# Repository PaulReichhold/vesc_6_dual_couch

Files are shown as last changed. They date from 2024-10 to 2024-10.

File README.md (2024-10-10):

# Compact High Power Motor Controller
Based on the VESC-Project of Benjamin Vedder

## Specs
| Spec | Tested to |
|---|---|
|__Voltage:__| 6.5V - 50.4V |
|__max Phase Current:__| 180A |
|__max Power (dual, with active cooling)__| 15kW |

> [!NOTE]
> One side has the current measurment inverted (forgot which one it was)

> [!WARNING]
> Use the provided design at your own risk

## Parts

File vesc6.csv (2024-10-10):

Source: | C:\Users\paulr\vesc_6_2\vesc6.kicad_sch
Date: | 16.02.2024 15:32:52
Tool: | Eeschema 7.0.10
Generator: | C:\Program Files\KiCad\7.0\bin\scripting\plugins/bom_csv_grouped_by_value.py
Component Count: | 129
Collated Components:
Item | Qty | Reference(s) | Value | LibPart | Footprint | Datasheet | DNP | LCSC-PN | Voltage
1 | 1 | C3 | 100n | Device:C_Small | Capacitor_SMD:C_0603_1608Metric | ~ |  |  | 50V
2 | 16 | C5, C6, C7, C8, C9, C12, C20, C23, C26, C27, C35, C36, C38, C44, C51, C57 | 100n | Device:C | Capacitor_SMD:C_0603_1608Metric | ~ |  |  | 50V
3 | 2 | C10, C11 | 15p | Device:C | Capacitor_SMD:C_0603_1608Metric | ~ |  |  | 50V
4 | 2 | C13, C14 | 1u | Device:C | Capacitor_SMD:C_0603_1608Metric | ~ |  |  | 50V
5 | 1 | C15 | 6n8 | Device:C | Capacitor_SMD:C_0603_1608Metric | ~ |  |  | 100V
6 | 5 | C16, C17, C18, C21, C33 | 2.2u | Device:C | Capacitor_SMD:C_0805_2012Metric | ~ |  |  | 100V
7 | 1 | C19 | 120p | Device:C | Capacitor_SMD:C_0603_1608Metric | ~ |  |  | 100V
8 | 1 | C22 | 22n | Device:C | Capacitor_SMD:C_0603_1608Metric | ~ |  |  | 100V
9 | 4 | C24, C39, C46, C52 | 15n | Device:C | Capacitor_SMD:C_0603_1608Metric | ~ |  |  | 100V
10 | 3 | C25, C31, C32 | 4.7u | Device:C | Capacitor_SMD:C_1206_3216Metric | ~ |  |  | 100V
11 | 3 | C28, C29, C30 | 220n | Device:C | Capacitor_SMD:C_0805_2012Metric | ~ |  |  | 100V
12 | 2 | C34, C37 | 100u | Device:C_Polarized | Capacitor_Tantalum_SMD:CP_EIA-3528-21_Kemet-B | ~ |  |  | 16V
13 | 3 | C40, C48, C53 | 1n | Device:C | Capacitor_SMD:C_0603_1608Metric | ~ |  |  | 100V
14 | 6 | C41, C42, C49, C50, C54, C55 | 4.7u | Device:C | Capacitor_SMD:C_1210_3225Metric | ~ |  |  | 100V
15 | 3 | C43, C45, C47 | 470u | Device:C_Polarized | Capacitor_THT:CP_Radial_D12.5mm_P5.00mm | ~ |  |  | 80V
16 | 2 | C56, C58 | 22u | Device:C_Polarized | Capacitor_SMD:CP_Elec_8x6.2 | https://datasheet.lcsc.com/lcsc/2304140030_Nichicon-UCD1J220MCL6GS_C445454.pdf |  | C445454 | 63V
17 | 1 | D5 | GRN | Device:LED | LED_SMD:LED_0603_1608Metric_Pad1.05x0.95mm_HandSolder | ~
18 | 1 | D6 | RED | Device:LED | LED_SMD:LED_0603_1608Metric_Pad1.05x0.95mm_HandSolder | ~
19 | 1 | D7 | BLU | Device:LED | LED_SMD:LED_0603_1608Metric_Pad1.05x0.95mm_HandSolder | ~
20 | 1 | D8 | D_Schottky | Device:D_Schottky | Diode_SMD:D_SOD-128 | https://datasheet.lcsc.com/lcsc/2004031108_Nexperia-PMEG10030ELP_C503376.pdf |  | C503376
21 | 1 | D9 | 5V | Device:D_TVS | Diode_SMD:D_SOD-128 | https://datasheet.lcsc.com/lcsc/2304140030_Nexperia-PTVS5V0P1UP-115_C426873.pdf |  | C426873
22 | 1 | FB1 | FerriteBead | Device:FerriteBead | Resistor_SMD:R_1206_3216Metric | https://datasheet.lcsc.com/lcsc/2305221646_YJYCOIN-YI321611U601-3R0T_C2858472.pdf |  | C2858472 | 100V
23 | 1 | J1 | Main | Connector_Generic:Conn_01x03 | Connector_PinSocket_2.54mm:PinSocket_1x03_P2.54mm_Vertical | ~
24 | 1 | J2 | HALL_ENC | Connector_Generic:Conn_01x06 | Connector_JST:JST_PH_B6B-PH-K_1x06_P2.00mm_Vertical | ~
25 | 1 | J6 | USB | Connector:USB_OTG | Connector_USB:USB_Micro-B_Wuerth_614105150721_Vertical_CircularHoles | ~
26 | 1 | L1 | 22u | Device:L | Inductor_SMD:L_Bourns-SRN4018 | https://datasheet.lcsc.com/lcsc/2201121400_SHOU-HAN-CY43-22UH_C2929420.pdf |  | C2929420
27 | 1 | Q1 | DMN62D0UW | Device:Q_NMOS_GSD | Package_TO_SOT_SMD:SOT-323_SC-70 | https://datasheet.lcsc.com/lcsc/2308101701_Diodes-Incorporated-DMN62D0UWQ-7_C5248878.pdf |  | C5248878
28 | 6 | Q2, Q3, Q4, Q5, Q6, Q7 | HYG015N10NS1TA | Device:Q_NMOS_GSD | Package_TO_SOT_SMD:Infineon_PG-HSOF-8-1 | ~ |  | C2979263
29 | 7 | R6, R7, R8, R21, R25, R27, R29 | 2.2k | Device:R | Resistor_SMD:R_0603_1608Metric | ~
30 | 1 | R10 | 0 | Device:R | Resistor_SMD:R_0603_1608Metric | ~
31 | 3 | R11, R23, R30 | 10k | Device:R | Resistor_SMD:R_0603_1608Metric | ~
32 | 2 | R12, R13 | 22 | Device:R | Resistor_SMD:R_0603_1608Metric | ~
33 | 2 | R14, R15 | 220 | Device:R | Resistor_SMD:R_0603_1608Metric | ~
34 | 4 | R16, R34, R38, R40 | 1k | Device:R | Resistor_SMD:R_0603_1608Metric | ~
35 | 1 | R17 | 3.3k | Device:R | Resistor_SMD:R_0603_1608Metric | ~
36 | 1 | R18 | 18k | Device:R | Resistor_SMD:R_0603_1608Metric | ~
37 | 1 | R19 | 15k | Device:R | Resistor_SMD:R_0603_1608Metric | ~
38 | 3 | R20, R24, R26 | 39k | Device:R | Resistor_SMD:R_0603_1608Metric | ~
39 | 1 | R22 | 220k | Device:R | Resistor_SMD:R_0603_1608Metric | ~
40 | 1 | R28 | 39K | Device:R | Resistor_SMD:R_0603_1608Metric | ~
41 | 3 | R31, R35, R39 | 0.5m | Device:R_Shunt | TUWR_Sensors:BVN_1216 | https://datasheet.lcsc.com/lcsc/2103091535_Isabellenhuette-BVN-Z-R0005-1-0_C2688874.pdf |  | C2688874
42 | 6 | R32, R33, R36, R37, R41, R42 | 4.7 | Device:R | Resistor_SMD:R_0603_1608Metric | ~
43 | 1 | R43 | 120 | Device:R | Resistor_SMD:R_0603_1608Metric | ~
44 | 1 | SW1 | SENS_VOLTAGE | Switch:SW_Push_SPDT | Jumper:SolderJumper-3_P1.3mm_Bridged2Bar12_Pad1.0x1.5mm | ~
45 | 1 | TH1 | NTC | Device:Thermistor_NTC | Connector_PinHeader_1.27mm:PinHeader_1x02_P1.27mm_Vertical | ~
46 | 1 | TP1 | SWCLK | Connector:TestPoint | TestPoint:TestPoint_Pad_D1.0mm | ~
47 | 1 | TP2 | SWDIO | Connector:TestPoint | TestPoint:TestPoint_Pad_D1.0mm | ~
48 | 1 | TP3 | NRST | Connector:TestPoint | TestPoint:TestPoint_Pad_D1.0mm | ~
49 | 1 | TP4 | GND | Connector:TestPoint | TestPoint:TestPoint_Pad_D1.0mm | ~
50 | 1 | U1 | STM32F405RGTx | MCU_ST_STM32F4:STM32F405RGTx | Package_QFP:LQFP-64_10x10mm_P0.5mm | http://www.st.com/st-web-ui/static/active/en/resource/technical/document/datasheet/DM00037051.pdf |  | C15742
51 | 6 | U2, U4, U5, U8, U9, U11 | Mc74VHC1GT66 | TUWR_IC:Mc74VHC1GT66 | Package_TO_SOT_SMD:SOT-353_SC-70-5 | https://www.lcsc.com/product-detail/span-style-background-color-ff0-Analog-span-Switches-Multiplexers_Texas-Instruments-SN74LVC1G66DCKR_C113518.html |  | C113518
52 | 1 | U3 | DRV8301DCAR | 2023-03-11_13-45-03:DRV8301DCAR | Package_SO:HTSSOP-56-1EP_6.1x14mm_P0.5mm_EP3.61x6.35mm | https://datasheet.lcsc.com/lcsc/1808280253_Texas-Instruments-DRV8301DCAR_C98969.pdf |  | C98969
53 | 1 | U6 | TLV73333PDBV | Regulator_Linear:TLV73333PDBV | Package_TO_SOT_SMD:SOT-23-5 | http://www.ti.com/lit/ds/symlink/tlv733p.pdf |  | C134139
54 | 3 | U7, U10, U12 | AD8418 | Amplifier_Current:AD8418 | Package_SO:MSOP-8_3x3mm_P0.65mm | https://www.analog.com/media/en/technical-documentation/data-sheets/AD8418.pdf |  | C147928
55 | 1 | U14 | SN65HVD232 | Interface_CAN_LIN:SN65HVD232 | Package_SO:SOIC-8_3.9x4.9mm_P1.27mm | https://datasheet.lcsc.com/lcsc/1810181615_Texas-Instruments-SN65HVD232DR_C30530.pdf |  | C30530
56 | 1 | Y1 | 8M | Device:Crystal_GND24 | Crystal:Crystal_SMD_EuroQuartz_MT-4Pin_3.2x2.5mm_HandSoldering | ~

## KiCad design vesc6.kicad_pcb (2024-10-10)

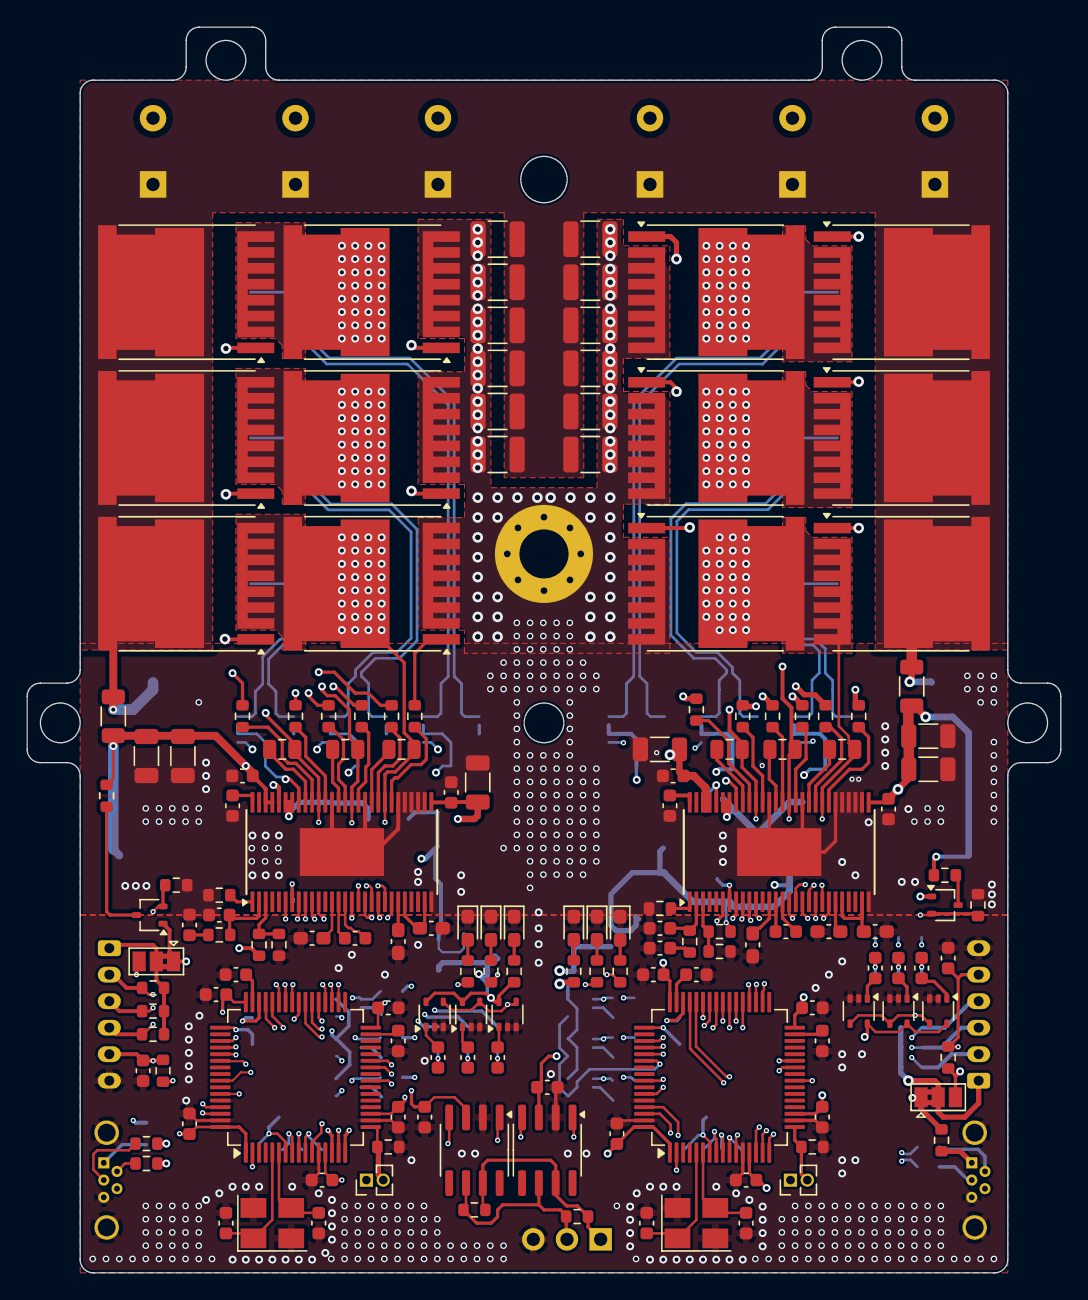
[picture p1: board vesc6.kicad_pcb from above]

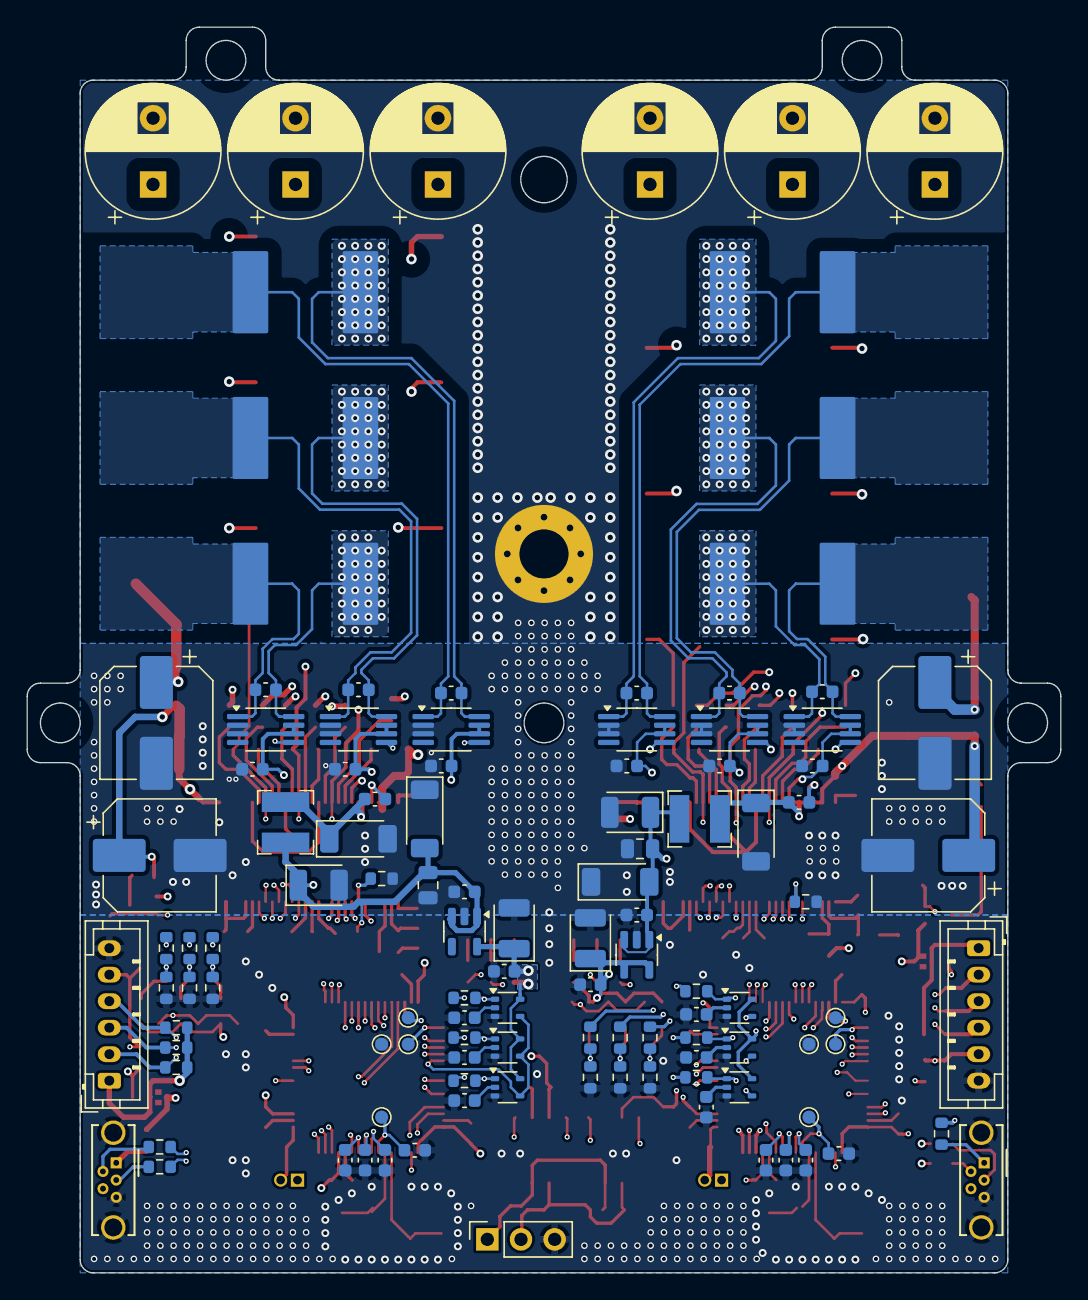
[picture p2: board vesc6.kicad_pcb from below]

Board: 4 copper layers, 78.0 x 94.0 mm, 266 parts (113 on the bottom side), 190 nets.

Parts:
C1, C2, C3, C4, C5, C6, C7, C8, C9, C12, C20, C23, C26, C27, C35, C36, C38, C44, C51, C57, C59, C69, C77, C82, C83, C84, C85, C86, C89, C94, C99, C101, C102, C106, C108, C114, C116, C118: 100n; C_0603_1608Metric
C10, C11, C87, C88: 15p; C_0603_1608Metric
C13, C14, C90, C91: 1u; C_0603_1608Metric
C15, C93: 6n8; C_0603_1608Metric
C16, C40, C48, C53, C61, C62, C63, C64, C68, C73, C76, C79: 1n; C_0603_1608Metric
C17, C18, C21, C92, C96, C98: 2.2u; C_0603_1608Metric_Pad1.08x0.95mm_HandSolder
C19, C97: 120p; C_0603_1608Metric
C22, C95: 22n; C_0603_1608Metric
C24, C39, C46, C52, C60, C71, C78, C100: 15n; C_0603_1608Metric
C25, C31, C32, C107, C109, C110: 4.7u; C_1206_3216Metric
C28, C29, C30, C103, C104, C105: 220n; C_0805_2012Metric
C33, C111: 2.2u; C_0805_2012Metric
C34, C37, C113, C117: 100u; CP_EIA-3528-21_Kemet-B
C41, C42, C49, C50, C54, C55, C65, C66, C74, C75, C80, C81: 4.7u; C_1210_3225Metric
C43, C45, C47, C67, C70, C72: 470u; CP_Radial_D10.0mm_P5.00mm
C56, C58, C112, C115: 22u; CP_Elec_8x6.2
D1, D5: GRN; LED_0603_1608Metric_Pad1.05x0.95mm_HandSolder
D2, D6: RED; LED_0603_1608Metric_Pad1.05x0.95mm_HandSolder
D3, D7: BLU; LED_0603_1608Metric_Pad1.05x0.95mm_HandSolder
D4, D8: D_Schottky; D_SOD-128
D9, D10: 5V; D_SOD-128
FB1, FB2: FerriteBead; R_1206_3216Metric
H1: MountingHole_Pad; MountingHole_3.7mm_Pad_Via
J1: Main; PinSocket_1x03_P2.54mm_Vertical
J2, J3: HALL_ENC; JST_PH_B6B-PH-K_1x06_P2.00mm_Vertical
J4, J6: USB; USB_Micro-B_Wuerth_614105150721_Vertical_CircularHoles
L1, L2: 22u; L_Bourns-SRN4018
Q1, Q14: DMN62D0UW; SOT-323_SC-70
Q2, Q3, Q4, Q5, Q6, Q7, Q8, Q9, Q10, Q11, Q12, Q13: HYG015N10NS1TA; Infineon_PG-HSOF-8-1
R1, R2, R3, R49, R53, R57: 0.5m; WSLP3921
R4, R5, R6, R7, R8, R9, R21, R25, R27, R29, R65, R69, R71, R73: 2.2k; R_0603_1608Metric
R10, R31: 0; R_0603_1608Metric
R11, R23, R30, R35, R48, R67: 10k; R_0603_1608Metric
R12, R13, R39, R44: 22; R_0603_1608Metric
R14, R15, R45, R46: 220; R_0603_1608Metric
R16, R34, R38, R40, R47, R52, R56, R58: 1k; R_0603_1608Metric
R17, R61: 3.3k; R_0603_1608Metric
R18, R62: 18k; R_0603_1608Metric
R19, R63: 15k; R_0603_1608Metric
R20, R24, R26, R64, R68, R70: 39k; R_0603_1608Metric
R22, R66: 220k; R_0603_1608Metric
R28, R72: 39K; R_0603_1608Metric
R32, R33, R36, R37, R41, R42, R50, R51, R54, R55, R59, R60: 4.7; R_0603_1608Metric
R43, R74: 120; R_0603_1608Metric
SW1, SW2: SENS_VOLTAGE; SolderJumper-3_P1.3mm_Bridged2Bar12_Pad1.0x1.5mm
TH1, TH2: NTC; PinHeader_1x02_P1.27mm_Vertical
TP1, TP5: SWCLK; TestPoint_Pad_D1.0mm
TP2, TP6: SWDIO; TestPoint_Pad_D1.0mm
TP3, TP7: NRST; TestPoint_Pad_D1.0mm
TP4, TP8: GND; TestPoint_Pad_D1.0mm
U1, U20: STM32F405RGTx; LQFP-64_10x10mm_P0.5mm
U2, U4, U5, U8, U9, U11, U15, U16, U18, U21, U23, U24: Mc74VHC1GT66; SOT-353_SC-70-5
U3, U22: DRV8301DCAR; HTSSOP-56-1EP_6.1x14mm_P0.5mm_EP3.61x6.35mm
U6, U25: TLV73333PDBV; SOT-23-5
U7, U10, U12, U13, U17, U19: AD8418; MSOP-8_3x3mm_P0.65mm
U14, U26: SN65HVD232; SOIC-8_3.9x4.9mm_P1.27mm
Y1, Y2: 8M; Crystal_SMD_EuroQuartz_MT-4Pin_3.2x2.5mm_HandSoldering

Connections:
/VESC_Left/3.3V: C5.1, C6.1, C7.1, C8.1, C9.1, C36.1, C37.1, C38.2, C44.2, C51.2, C57.1, R11.2, R16.2, SW1.3 (C), TH1.1, U1.1 (VBAT), U1.13 (VDDA), U1.19 (VDD), U1.32 (VDD), U1.48 (VDD), U1.64 (VDD), U2.5 (VCC), U3.49 (VDD_SPI), U4.5 (VCC), U5.5 (VCC), U6.5 (OUT), U7.6 (VS), U7.7 (REF1), U8.5 (VCC), U9.5 (VCC), U10.6 (VS), U10.7 (REF1), U11.5 (VCC), U12.6 (VS), U12.7 (REF1), U14.3 (VCC)
/VESC_Left/5V: C33.1, C34.1, C35.1, D9.2 (A2), L1.2, Q1.1 (G), R10.2, R18.2, SW1.1 (A), U6.1 (IN), U6.3 (EN)
/VESC_Left/CAN/RX: U1.61 (PB8), U14.4 (R)
/VESC_Left/CAN/TX: U1.62 (PB9), U14.1 (D)
/VESC_Left/CAN_H: J1.1, R43.1, R74.1, U14.7 (CANH), U26.7 (CANH)
/VESC_Left/CAN_L: J1.2, R43.2, R74.2, U14.6 (CANL), U26.6 (CANL)
/VESC_Left/DRV8301/CS: U1.40 (PC9), U3.8 (*SCS)
/VESC_Left/DRV8301/EN_GATE: U1.57 (PB5), U3.16 (EN_GATE)
/VESC_Left/DRV8301/FAULT: U1.59 (PB7), U3.6 (*FAULT)
/VESC_Left/DRV8301/GH_A: R32.1, U3.47 (GH_A)
/VESC_Left/DRV8301/GH_B: R36.1, U3.42 (GH_B)
/VESC_Left/DRV8301/GH_C: R41.1, U3.37 (GH_C)
/VESC_Left/DRV8301/GL_A: R33.1, U3.45 (GL_A)
/VESC_Left/DRV8301/GL_B: R37.1, U3.40 (GL_B)
/VESC_Left/DRV8301/GL_C: R42.1, U3.35 (GL_C)
/VESC_Left/DRV8301/INH_A: U1.41 (PA8), U3.17 (INH_A)
/VESC_Left/DRV8301/INH_B: U1.42 (PA9), U3.19 (INH_B)
/VESC_Left/DRV8301/INH_C: U1.43 (PA10), U3.21 (INH_C)
/VESC_Left/DRV8301/INL_A: U1.34 (PB13), U3.18 (INL_A)
/VESC_Left/DRV8301/INL_B: U1.35 (PB14), U3.20 (INL_B)
/VESC_Left/DRV8301/INL_C: U1.36 (PB15), U3.22 (INL_C)
/VESC_Left/DRV8301/SCLK: U1.51 (PC10), U3.11 (SCLK)
/VESC_Left/DRV8301/SDI: U1.53 (PC12), U3.9 (SDI)
/VESC_Left/DRV8301/SDO: U1.52 (PC11), U3.10 (SDO)
/VESC_Left/DRV8301/SENS_A: C20.1, R20.2, R21.2, U1.14 (PA0)
/VESC_Left/DRV8301/SENS_B: C23.1, R24.2, R25.2, U1.15 (PA1)
/VESC_Left/DRV8301/SENS_C: C26.1, R26.2, R27.2, U1.16 (PA2)
/VESC_Left/DRV8301/SENS_FILTERED: U1.2 (PC13), U2.4 (ON_OFF), U4.4 (ON_OFF), U5.4 (ON_OFF)
/VESC_Left/DRV8301/SENS_SUPPLY: Q1.2 (S), R29.1, U1.11 (PC3)
/VESC_Left/DRV8301/Supply_Filterted: C1.1, C2.1, C25.1, C31.1, C32.1, C58.1, FB1.1, R28.1, U3.29 (PVDD1), U3.53 (PVDD2), U3.54 (PVDD2)
/VESC_Left/MCU/ADC_TEMP: R30.2, TH1.2, U1.17 (PA3)
/VESC_Left/MCU/CURRENT_1: C40.2, R34.1, U1.8 (PC0), U8.1 (IO_XA)
/VESC_Left/MCU/CURRENT_2: C48.2, R38.1, U1.9 (PC1), U9.1 (IO_XA)
/VESC_Left/MCU/CURRENT_3: C53.2, R40.1, U1.10 (PC2), U11.1 (IO_XA)
/VESC_Left/MCU/CURR_FILTER_ON: U1.54 (PD2), U8.4 (ON_OFF), U9.4 (ON_OFF), U11.4 (ON_OFF)
/VESC_Left/MCU/HALL_1: J2.2, R6.2, U1.37 (PC6)
/VESC_Left/MCU/HALL_2: J2.3, R7.2, U1.38 (PC7)
/VESC_Left/MCU/HALL_3: J2.4, R8.2, U1.39 (PC8)
/VESC_Left/MCU/LED_GREEN: R14.2, U1.26 (PB0)
/VESC_Left/MCU/LED_RED: R15.2, U1.27 (PB1)
/VESC_Left/MCU/NRST: C12.1, TP3.1, U1.7 (NRST)
/VESC_Left/MCU/SWCLK: TP1.1, U1.49 (PA14)
/VESC_Left/MCU/SWDIO: TP2.1, U1.46 (PA13)
/VESC_Left/MCU/TEMP_MOTOR: C3.1, J2.5, R11.1, U1.24 (PC4)
/VESC_Left/MCU/USB_D_N: R13.2, U1.44 (PA11)
/VESC_Left/MCU/USB_D_P: R12.2, U1.45 (PA12)
/VESC_Left/Power_alternate/C_A: R34.2, U7.5 (OUT)
/VESC_Left/Power_alternate/C_B: R38.2, U10.5 (OUT)
/VESC_Left/Power_alternate/C_C: R40.2, U12.5 (OUT)
/VESC_Left/Power_alternate/SH_A_N: C61.1, R1.2, U7.1 (IN-)
/VESC_Left/Power_alternate/SH_A_P: C28.1, C61.2, Q2.2 (S), Q3.3 (D), R1.1, R20.1, U3.46 (SH_A), U7.8 (IN+)
/VESC_Left/Power_alternate/SH_B_N: C62.1, R2.2, U10.1 (IN-)
/VESC_Left/Power_alternate/SH_B_P: C29.1, C62.2, Q4.2 (S), Q5.3 (D), R2.1, R24.1, U3.41 (SH_B), U10.8 (IN+)
/VESC_Left/Power_alternate/SH_C_N: C63.1, R3.2, U12.1 (IN-)
/VESC_Left/Power_alternate/SH_C_P: C30.1, C63.2, Q6.2 (S), Q7.3 (D), R3.1, R26.1, U3.36 (SH_C), U12.8 (IN+)
/VESC_Left/SUPPLY: C41.1, C42.1, C43.1, C45.1, C47.1, C49.1, C50.1, C54.1, C55.1, C56.1, C65.1, C66.1, C67.1, C70.1, C72.1, C74.1, C75.1, C80.1, C81.1, C115.1, FB1.2, FB2.2, Q2.3 (D), Q4.3 (D), Q6.3 (D), Q8.3 (D), Q10.3 (D), Q12.3 (D)
/VESC_Right/3.3V: C59.2, C69.2, C77.2, C82.1, C83.1, C84.1, C85.1, C86.1, C116.1, C117.1, C118.1, R35.2, R47.2, SW2.3 (C), TH2.1, U13.6 (VS), U13.7 (REF1), U15.5 (VCC), U16.5 (VCC), U17.6 (VS), U17.7 (REF1), U18.5 (VCC), U19.6 (VS), U19.7 (REF1), U20.1 (VBAT), U20.13 (VDDA), U20.19 (VDD), U20.32 (VDD), U20.48 (VDD), U20.64 (VDD), U21.5 (VCC), U22.49 (VDD_SPI), U23.5 (VCC), U24.5 (VCC), U25.5 (OUT), U26.3 (VCC)
/VESC_Right/5V: C111.1, C113.1, C114.1, D10.2 (A2), L2.2, Q14.1 (G), R31.2, R62.2, SW2.1 (A), U25.1 (IN), U25.3 (EN)
/VESC_Right/CAN/RX: U20.61 (PB8), U26.4 (R)
/VESC_Right/CAN/TX: U20.62 (PB9), U26.1 (D)
/VESC_Right/DRV8301/CS: U20.40 (PC9), U22.8 (*SCS)
/VESC_Right/DRV8301/EN_GATE: U20.57 (PB5), U22.16 (EN_GATE)
/VESC_Right/DRV8301/FAULT: U20.59 (PB7), U22.6 (*FAULT)
/VESC_Right/DRV8301/GH_A: R50.1, U22.47 (GH_A)
/VESC_Right/DRV8301/GH_B: R54.1, U22.42 (GH_B)
/VESC_Right/DRV8301/GH_C: R59.1, U22.37 (GH_C)
/VESC_Right/DRV8301/GL_A: R51.1, U22.45 (GL_A)
/VESC_Right/DRV8301/GL_B: R55.1, U22.40 (GL_B)
/VESC_Right/DRV8301/GL_C: R60.1, U22.35 (GL_C)
/VESC_Right/DRV8301/INH_A: U20.41 (PA8), U22.17 (INH_A)
/VESC_Right/DRV8301/INH_B: U20.42 (PA9), U22.19 (INH_B)
/VESC_Right/DRV8301/INH_C: U20.43 (PA10), U22.21 (INH_C)
/VESC_Right/DRV8301/INL_A: U20.34 (PB13), U22.18 (INL_A)
/VESC_Right/DRV8301/INL_B: U20.35 (PB14), U22.20 (INL_B)
/VESC_Right/DRV8301/INL_C: U20.36 (PB15), U22.22 (INL_C)
/VESC_Right/DRV8301/SCLK: U20.51 (PC10), U22.11 (SCLK)
/VESC_Right/DRV8301/SDI: U20.53 (PC12), U22.9 (SDI)
/VESC_Right/DRV8301/SDO: U20.52 (PC11), U22.10 (SDO)
/VESC_Right/DRV8301/SENS_A: C94.1, R64.2, R65.2, U20.14 (PA0)
/VESC_Right/DRV8301/SENS_B: C99.1, R68.2, R69.2, U20.15 (PA1)
/VESC_Right/DRV8301/SENS_C: C101.1, R70.2, R71.2, U20.16 (PA2)
/VESC_Right/DRV8301/SENS_FILTERED: U20.2 (PC13), U21.4 (ON_OFF), U23.4 (ON_OFF), U24.4 (ON_OFF)
/VESC_Right/DRV8301/SENS_SUPPLY: Q14.2 (S), R73.1, U20.11 (PC3)
/VESC_Right/DRV8301/Supply_Filterted: C106.1, C107.1, C108.1, C109.1, C110.1, C112.1, FB2.1, R72.1, U22.29 (PVDD1), U22.53 (PVDD2), U22.54 (PVDD2)
/VESC_Right/MCU/ADC_TEMP: R48.2, TH2.2, U20.17 (PA3)
/VESC_Right/MCU/CURRENT_1: C64.2, R52.1, U15.1 (IO_XA), U20.8 (PC0)
/VESC_Right/MCU/CURRENT_2: C73.2, R56.1, U16.1 (IO_XA), U20.9 (PC1)
/VESC_Right/MCU/CURRENT_3: C79.2, R58.1, U18.1 (IO_XA), U20.10 (PC2)
/VESC_Right/MCU/CURR_FILTER_ON: U15.4 (ON_OFF), U16.4 (ON_OFF), U18.4 (ON_OFF), U20.54 (PD2)
/VESC_Right/MCU/HALL_1: J3.2, R4.2, U20.37 (PC6)
/VESC_Right/MCU/HALL_2: J3.3, R5.2, U20.38 (PC7)
/VESC_Right/MCU/HALL_3: J3.4, R9.2, U20.39 (PC8)
/VESC_Right/MCU/LED_GREEN: R45.2, U20.26 (PB0)
/VESC_Right/MCU/LED_RED: R46.2, U20.27 (PB1)
/VESC_Right/MCU/NRST: C89.1, TP7.1, U20.7 (NRST)
/VESC_Right/MCU/SWCLK: TP5.1, U20.49 (PA14)
/VESC_Right/MCU/SWDIO: TP6.1, U20.46 (PA13)
/VESC_Right/MCU/TEMP_MOTOR: C4.1, J3.5, R35.1, U20.24 (PC4)
/VESC_Right/MCU/USB_D_N: R44.2, U20.44 (PA11)
/VESC_Right/MCU/USB_D_P: R39.2, U20.45 (PA12)
/VESC_Right/Power/C_A: R52.2, U13.5 (OUT)
/VESC_Right/Power/C_B: R56.2, U17.5 (OUT)
/VESC_Right/Power/C_C: R58.2, U19.5 (OUT)
/VESC_Right/Power/SH_A_N: C16.2, R57.2, U13.8 (IN+)
/VESC_Right/Power/SH_A_P: C16.1, C103.1, Q8.2 (S), Q9.3 (D), R57.1, R64.1, U13.1 (IN-), U22.46 (SH_A)
/VESC_Right/Power/SH_B_N: C68.2, R53.2, U17.8 (IN+)
/VESC_Right/Power/SH_B_P: C68.1, C104.1, Q10.2 (S), Q11.3 (D), R53.1, R68.1, U17.1 (IN-), U22.41 (SH_B)
/VESC_Right/Power/SH_C_N: C76.2, R49.2, U19.8 (IN+)
/VESC_Right/Power/SH_C_P: C76.1, C105.1, Q12.2 (S), Q13.3 (D), R49.1, R70.1, U19.1 (IN-), U22.36 (SH_C)
GND: C1.2, C2.2, C3.2, C4.2, C5.2, C6.2, C7.2, C8.2, C9.2, C10.2, C11.2, C12.2, C13.2, C14.2, C15.2, C17.2, C18.2, C19.2, C21.2, C24.1, C25.2, C31.2, C32.2, C33.2, C34.2, C35.2, C36.2, C37.2, C38.1, C39.1, C40.1, C41.2, C42.2, C43.2, C44.1, C45.2, C46.1, C47.2, C48.1, C49.2, C50.2, C51.1, C52.1, C53.1, C54.2, C55.2, C56.2, C57.2, C58.2, C59.1, C60.1, C64.1, C65.2, C66.2, C67.2, C69.1, C70.2, C71.1, C72.2, C73.1, C74.2, C75.2, C77.1, C78.1, C79.1, C80.2, C81.2, C82.2, C83.2, C84.2, C85.2, C86.2, C87.2, C88.2, C89.2, C90.2, C91.2, C92.2, C93.2, C96.2, C97.2, C98.2, C100.1, C106.2, C107.2, C108.2, C109.2, C110.2, C111.2, C112.2, C113.2, C114.2, C115.2, C116.2, C117.2, C118.2, D1.1 (K), D2.1 (K), D3.1 (K), D4.2 (A), D5.1 (K), D6.1 (K), D7.1 (K), D8.2 (A), D9.1 (A1), D10.1 (A1), H1.1, J1.3, J2.6, J3.6, J4.5 (GND), J4.6 (Shield), J6.5 (GND), J6.6 (Shield), Q3.2 (S), Q5.2 (S), Q7.2 (S), Q9.2 (S), Q11.2 (S), Q13.2 (S), R17.1, R21.1, R22.1, R23.2, R25.1, R27.1, R29.2, R30.1, R48.1, R61.1, R65.1, R66.1, R67.2, R69.1, R71.1, R73.2, TP4.1, TP8.1, U1.12 (VSSA), U1.18 (VSS), U1.60 (BOOT0), U1.63 (VSS), U2.2 (IO_YA), U2.3 (GND), U3.28 (AGND), U3.30 (SP2), U3.31 (SN2), U3.32 (SP1), U3.33 (SN1), U3.34 (SL_C), U3.39 (SL_B), U3.44 (SL_A), U3.57 (EPAD), U4.2 (IO_YA), U4.3 (GND), U5.2 (IO_YA), U5.3 (GND), U6.2 (GND), U7.2 (GND), U7.3 (REF2), U8.3 (GND), U9.3 (GND), U10.2 (GND), U10.3 (REF2), U11.3 (GND), U12.2 (GND), U12.3 (REF2), U13.2 (GND), U13.3 (REF2), U14.2 (GND), U15.3 (GND), U16.3 (GND), U17.2 (GND), U17.3 (REF2), U18.3 (GND), U19.2 (GND), U19.3 (REF2), U20.12 (VSSA), U20.18 (VSS), U20.60 (BOOT0), U20.63 (VSS), U21.2 (IO_YA), U21.3 (GND), U22.28 (AGND), U22.30 (SP2), U22.31 (SN2), U22.32 (SP1), U22.33 (SN1), U22.34 (SL_C), U22.39 (SL_B), U22.44 (SL_A), U22.57 (EPAD), U23.2 (IO_YA), U23.3 (GND), U24.2 (IO_YA), U24.3 (GND), U25.2 (GND), U26.2 (GND), Y1.2, Y1.4, Y2.2, Y2.4
unnamed: C15.1, R19.1
unnamed: C93.1, R63.1
unnamed: D1.2 (A), R45.1
unnamed: D2.2 (A), R46.1
unnamed: D3.2 (A), R47.1
unnamed: C102.1, D4.1 (K), L2.1, U22.50 (PH), U22.51 (PH)
unnamed: D5.2 (A), R14.1
unnamed: D6.2 (A), R15.1
unnamed: D7.2 (A), R16.1
unnamed: C27.1, D8.1 (K), L1.1, U3.50 (PH), U3.51 (PH)
unnamed: J2.1, R6.1, R7.1, R8.1, SW1.2 (B)
unnamed: J3.1, R4.1, R5.1, R9.1, SW2.2 (B)
unnamed: J4.3 (D+), R39.1
unnamed: J4.2 (D-), R44.1
unnamed: J4.1 (VBUS), R31.1
unnamed: J6.3 (D+), R12.1
unnamed: J6.2 (D-), R13.1
unnamed: J6.1 (VBUS), R10.1
unnamed: Q1.3 (D), R28.2
unnamed: Q2.1 (G), R32.2
unnamed: Q3.1 (G), R33.2
unnamed: Q4.1 (G), R36.2
unnamed: Q5.1 (G), R37.2
unnamed: Q6.1 (G), R41.2
unnamed: Q7.1 (G), R42.2
unnamed: Q8.1 (G), R50.2
unnamed: Q9.1 (G), R51.2
unnamed: Q10.1 (G), R54.2
unnamed: Q11.1 (G), R55.2
unnamed: Q12.1 (G), R59.2
unnamed: Q13.1 (G), R60.2
unnamed: Q14.3 (D), R72.2
unnamed: C10.1, U1.5 (PH0), Y1.1
unnamed: C11.1, U1.6 (PH1), Y1.3
unnamed: C13.1, U1.31 (VCAP_1)
unnamed: C14.1, U1.47 (VCAP_2)
unnamed: C20.2, U2.1 (IO_XA)
unnamed: C21.1, U3.24 (REF), U3.27 (AVDD)
unnamed: C28.2, U3.48 (BST_A)
unnamed: C29.2, U3.43 (BST_B)
unnamed: C27.2, U3.52 (BST_BK)
unnamed: C30.2, U3.38 (BST_C)
unnamed: C19.1, R19.2, U3.2 (COMP)
unnamed: C22.1, U3.14 (CP1)
unnamed: C22.2, U3.15 (CP2)
unnamed: R23.1, U3.7 (DTC)
unnamed: C18.1, U3.23 (DVDD)
unnamed: C17.1, U3.13 (GVDD)
unnamed: R22.2, U3.1 (RT_CLK)
unnamed: C24.2, U3.56 (SS_TR)
unnamed: R17.2, R18.1, U3.3 (VSENSE)
unnamed: C23.2, U4.1 (IO_XA)
unnamed: C26.2, U5.1 (IO_XA)
unnamed: C39.2, U8.2 (IO_YA)
unnamed: C46.2, U9.2 (IO_YA)
unnamed: C52.2, U11.2 (IO_YA)
unnamed: C60.2, U15.2 (IO_YA)
unnamed: C71.2, U16.2 (IO_YA)
unnamed: C78.2, U18.2 (IO_YA)
unnamed: C87.1, U20.5 (PH0), Y2.1
unnamed: C88.1, U20.6 (PH1), Y2.3
unnamed: C90.1, U20.31 (VCAP_1)
unnamed: C91.1, U20.47 (VCAP_2)
unnamed: C94.2, U21.1 (IO_XA)
unnamed: C98.1, U22.24 (REF), U22.27 (AVDD)
unnamed: C103.2, U22.48 (BST_A)
unnamed: C104.2, U22.43 (BST_B)
unnamed: C102.2, U22.52 (BST_BK)
unnamed: C105.2, U22.38 (BST_C)
unnamed: C97.1, R63.2, U22.2 (COMP)
unnamed: C95.1, U22.14 (CP1)
unnamed: C95.2, U22.15 (CP2)
unnamed: R67.1, U22.7 (DTC)
unnamed: C96.1, U22.23 (DVDD)
unnamed: C92.1, U22.13 (GVDD)
unnamed: R66.2, U22.1 (RT_CLK)
unnamed: C100.2, U22.56 (SS_TR)
unnamed: R61.2, R62.1, U22.3 (VSENSE)
unnamed: C99.2, U23.1 (IO_XA)
unnamed: C101.2, U24.1 (IO_XA)
